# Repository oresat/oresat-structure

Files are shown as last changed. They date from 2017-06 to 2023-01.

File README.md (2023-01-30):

# CURRENT MECHANICAL CAD MOVED TO ONSHAPE

This repository of SolidWorks files is deprecated as of May 2022. After the lauch of OreSat0 to SSO in March 2022, our team decided to move to OnShape because of its collaboration and branching tools. The CAD can be viewed, copied, and exported [here](https://cad.onshape.com/documents/48b910b46086e6b0e2315353/w/4aa305da7933618e47be15b5/e/c74689e568e124e331e7da22).

# DEPRECATED - OreSat Structure Repository - DEPRECATED
The OreSat project is being managed by the Portland State Aerospace Society (PSAS), an interdisciplinary student-led aerospace project in the Maseeh College of Engineering and Computer Science at Portland State University. PSAS is hundred or so open source space nerds, mostly undergraduates of all majors, some graduate students, a few faculty advisors, and mentors we call "industry advisors".

We're building all of OreSat from scratch. For the record, this is a _terrible_ idea. There are plenty of amazing commercial-off-the-shelf CubeSat kits and components out there. But they're not open source, they're a tad bit expensive, and we're an educational group that likes to DIY it anyway. In this repository, you can find the mechanical models of our subsystems: fly them as is, use them as a reference design, or hack them up to make them better! We look forward to seeing what you do with the OreSat bus.

To get started, visit the [Official Site](https://www.oresat.org) and the [OreSat Structure Wiki](https://github.com/oresat/oresat-structure/wiki)

## License 
Portland State Aerospace Society © 2018-2021 

You may redistribute and modify this documentation under the terms of the CERN OHL v2 [http://ohwr.org/cernohl](http://ohwr.org/cernohl).
This documentation is distributed WITHOUT ANY EXPRESS OR IMPLIED WARRANTY, INCLUDING OF MERCHANTABILITY, SATISFACTORY QUALITY AND FITNESS FOR A PARTICULAR PURPOSE. 
Please see the CERN OHL v2 for applicable conditions.

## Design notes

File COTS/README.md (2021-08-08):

# COTS (Commercial Off The Shelf)
Any CAD file for a non-custom part that you downloaded form some website should go in here.
This is basically just a bunch of fasteners and electrical connectors.

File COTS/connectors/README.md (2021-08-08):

# COTS/connectors
This is where you put CAD for electrical connectors.

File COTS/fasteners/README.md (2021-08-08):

# COTS/fasteners
This holds all the COTS parts that hold stuff together.
Part and assembly files shouldn't go in here;
they should go in one of the subfolders according to what kind of fastener they are.

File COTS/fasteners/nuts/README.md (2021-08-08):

# COTS/nuts
This holds nuts. You know what nuts are.
They have internal threads and go on the end of a bolt.
Standoffs are not nuts.

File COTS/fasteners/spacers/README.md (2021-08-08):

# COTS/spacers
This folder holds spacers. Spacers are *not* threaded. Washers are not spacers.

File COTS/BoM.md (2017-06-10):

# OreSat Bill of Materials
_Italic_ prices are variable with quantity. _Italic_ quantities are uncertain (either need to check the model or confer with ECEs).

item number and/or link | extended info sheet | cost per item | quantity per cubesat | description
---|---|---|---|---|---
[SamTec MMCX-J-P-H-RA-TH1][MMCX female] | [here][MMCX female location] | _3.40_ | _66_ | female right-angle radio-frequency connector (all on backplane)
[Samtec MMCX-P-P-H-ST-TH1][MMCX male] | [x][MMCX male location] | _4.58_ | _66_ | male straight radio-frequency connector (3 per card)
??? | [???] | ??? | _20_ | 40-pin female right-angle connector (power and data; 1 per card)
??? | [???] | ??? | _20_ | 40-pin male straight connector (power and data; all on backplane)
??? | [???] | ??? | _10_ | 20-pin female right-angle connector (power and data; _4_&_1_ or _5_ per end card?)
??? | [???] | ??? | _10_ | 20-pin male straight connector (power and data; 1 per solar card)
??? | [???] | ??? | ??? | #4-40 button screw
??? | [???] | ??? | ??? | #4-40 standoff
??? | [???] | ??? | ??? | #0-80 panhead screw
??? | [???] | ??? | ??? | #0-80 standoff
??? | [???] | ??? | ??? | #0-80 micro flat head

[MMCX female]: https://www.digikey.com/product-detail/en/samtec-inc/MMCX-J-P-H-RA-TH1/SAM10615-ND/6561608
[MMCV female location]: MMCX/MMCX_J_P_H_RA_TH1.md
[MMCX male]: https://www.digikey.com/product-detail/en/samtec-inc/MMCX-P-P-H-ST-TH1/SAM10618-ND/6561612
[MMCV male location]: MMCX/MMCX_male_straight.md

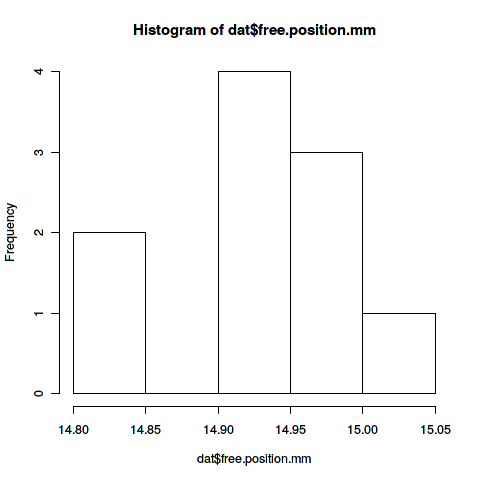
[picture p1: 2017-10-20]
COTS/other/ZFswitches/switchHist.png

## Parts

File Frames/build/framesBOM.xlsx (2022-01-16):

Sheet: 1U
PART NUMBER | DESCRIPTION | QTY.
1U_Frame | Y Frame | 2
1U_Frame | +X Frame | 1
1U_Frame | -X Frame | 1
OreSat_Ca rdWedge | Full Length Card Wedge | 14
+Xframe | +X Card Wedge | 5
OreSat_Ca rdWedgeTri angle | Full Length Card Wedge Triangle | 19
StarTracker Wedge | Star Tracker Wedge Triangle | 2
startracker wedge | +X Startracker Card Wedge | 2
92095A451 |  | 63
93600A061 | M1.5 DIA x 6 DOWEL PIN | 8
92290A060 | M2.5 x 0.45 x 10 Socket Head Screw | 8
91630A221 | M2.5 x 0.45 x 2.5 SCREW-LOCK HELICAL TANGLESS | 8
84985A46 | CPSLO cubesat.org Springs (Using Slotted Long- Nose Spring Plunger 8-36 in CAD) | 4

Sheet: 1.5U
PART NUMBER | DESCRIPTION | QTY.
1.5U_Frame |  | 2
1.5U_Frame |  | 1
1.5U_Frame |  | 1
92703A159 | M2.5 x 0.45 x 8 TORX FLAT HEAD SCREW | 10
92290A060 | M2.5 x 0.45 x 10 Socket Head Screw | 8
91630A221 | M2.5 x 0.45 x 2.5 SCREW-LOCK HELICAL TANGLESS | 8
93600A061 | M1.5 DIA x 6 DOWEL PIN | 8
90910A920 | M2 x 0.4 x 4 Button Head Screw | 69
+Xframecut | +X Card Wedge Cut | 1
+Xframe | +X Card Wedge | 5
startrackerwedge | +X Startracker Card Wedge | 2
OreSat_CardWedgeTr iangle | Full Length Card Wedge Triangle | 19
short | Short Triangle | 6
StarTrackerWedge | Star Tracker Wedge Triangle | 2
OreSat_CardWedge | Full Length Card Wedge | 14
WithCutout | Y Card Wedge Cut | 2
84985A46 | CPSLO cubesat.org Springs (Using Slotted Long-Nose Spring Plunger 8-36 in CAD) | 4

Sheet: 2U
PART NUMBER | DESCRIPTION | QTY.
2U_Frame | +X Frame | 1
2U_Frame | -X Frame | 1
2U_Frame | Y Frame | 2
90910A920 | M2 x 0.4 x 4 Button Head Screw | 111
93600A061 | M1.5 DIA x 6 DOWEL PIN | 8
92290A060 | M2.5 x 0.45 x 10 Socket Head Screw | 16
84985A46 | CPSLO cubesat.org Springs (Using Slotted Long-Nose Spring Plunger 8- 36 in CAD) | 4
92703A159 | M2.5 x 0.45 x 8 TORX FLAT HEAD SCREW | 10
91630A221 | M2.5 x 0.45 x 2.5 SCREW-LOCK HELICAL TANGLESS | 16
OreSat_CardWedge | Full Length Card Wedge | 24
WithCutout | Y Card Wedge Cut | 2
+Xframe | +X Card Wedge | 9
+Xframecut | +X Card Wedge Cut | 1
OreSat_CardWedgeTri angle | Full Length Card Wedge Triangle | 32
short | Short Triangle | 6
StarTrackerWedge | Star Tracker Wedge Triangle | 3
startrackerwedge | +X Startracker Card Wedge | 3

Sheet: 3U
PART NUMBER | DESCRIPTION | QTY.
84985A46 | CPSLO cubesat.org Springs (Using Slotted Long-Nose Spring Plunger 8- 36 in CAD) | 4
93600A061 | M1.5 DIA x 6 DOWEL PIN | 8
92290A060 | M2.5 x 0.45 x 10 Socket Head Screw | 24
3U_Frame | +X Frame | 1
3U_Frame | -X Frame | 1
3U_Frame | Y Frame | 2
OreSat_CardWedge | Full Length Card Wedge | 56
OreSat_CardWedgeTri angle | Full Length Card Wedge Triangle | 63
WithCutout | Y Card Wedge Cut | 4
short | Short Triangle | 12
90910A920 | M2 x 0.4 x 4 Button Head Screw | 219
+Xframe | +X Card Wedge | 7
+Xframecut | +X Card Wedge Cut | 4
startrackerwedge | +X Startracker Card Wedge | 4
StarTrackerWedge | Star Tracker Wedge Triangle | 4
92703A159 | M2.5 x 0.45 x 8 TORX FLAT HEAD SCREW | 10

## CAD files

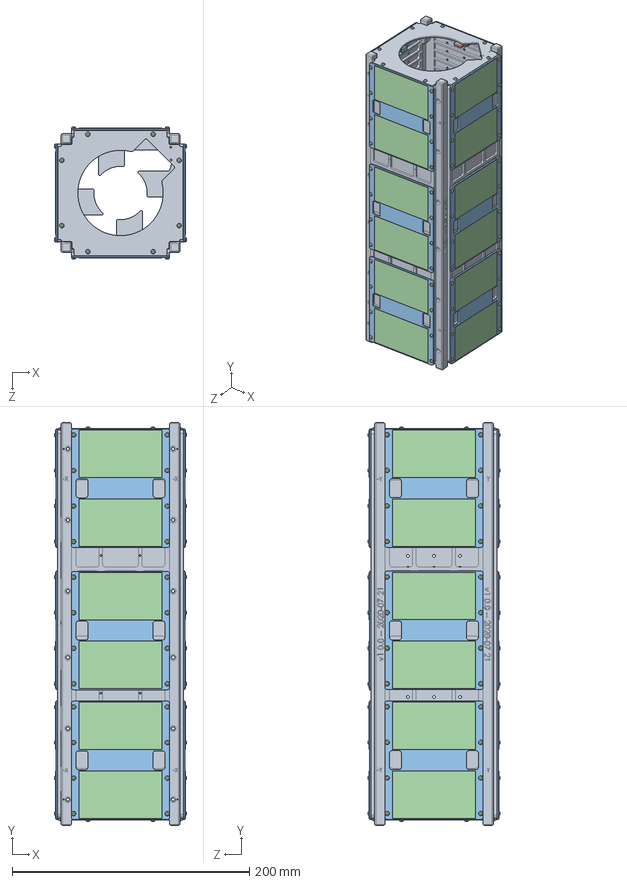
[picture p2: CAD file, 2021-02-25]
3UAssembly.SLDASM
111.4 x 340.0 x 111.4 mm
3U_Frame x 4
BackplaneBoardPCB_3U
M2x0.4x6mm_shoulderScrew_90278A431_18-8 STAINLESS STEEL PRECISION SHOULDER SCREW x 2
90910A920_LOW-PROFILE BUTTON HEAD TORX MACHINE SCREW x 140
Molex, LLC 0733000110 (Backplane) x 87
Molex 73300-0220 (Bullet) x 87
_SFM_120_01_L_D_LC_terminal_2 x 29
_C_20_01_D_pins_4 x 29
_SFM_110_03_L_D_LC_terminal_2 x 27
_C_10_03_D_pins_4 x 27
SolarModulePCB x 12
solarpanel x 24
M55-60212_MOULD.stp x 12
M55-602_CONTACT.stp x 144
M55-700_STRAP.stp x 24
EndCapPCB x 2

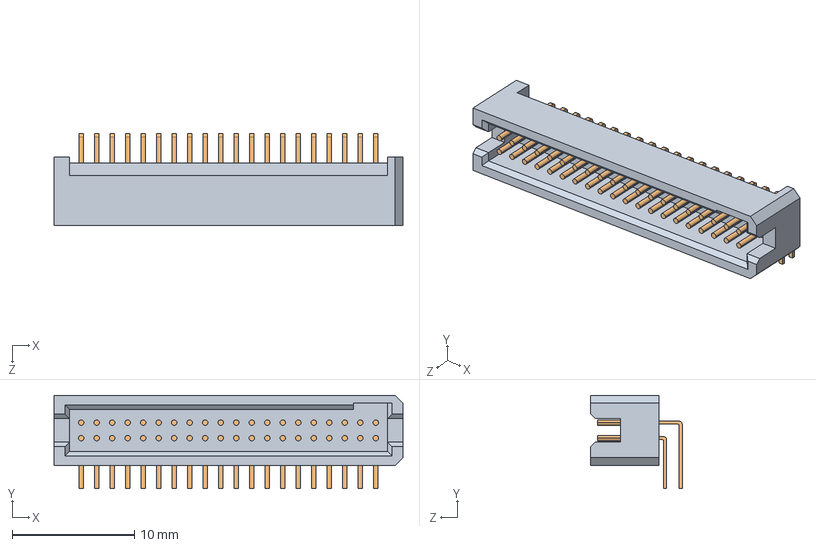
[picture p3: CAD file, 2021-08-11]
ADACS/OreSat0_ADACSCard.SLDASM
28.6 x 7.62 x 7.49 mm
_TFM_120_01_L_D_RA_terminal_2
_TFM_120_01_L_D_RA_pins_4

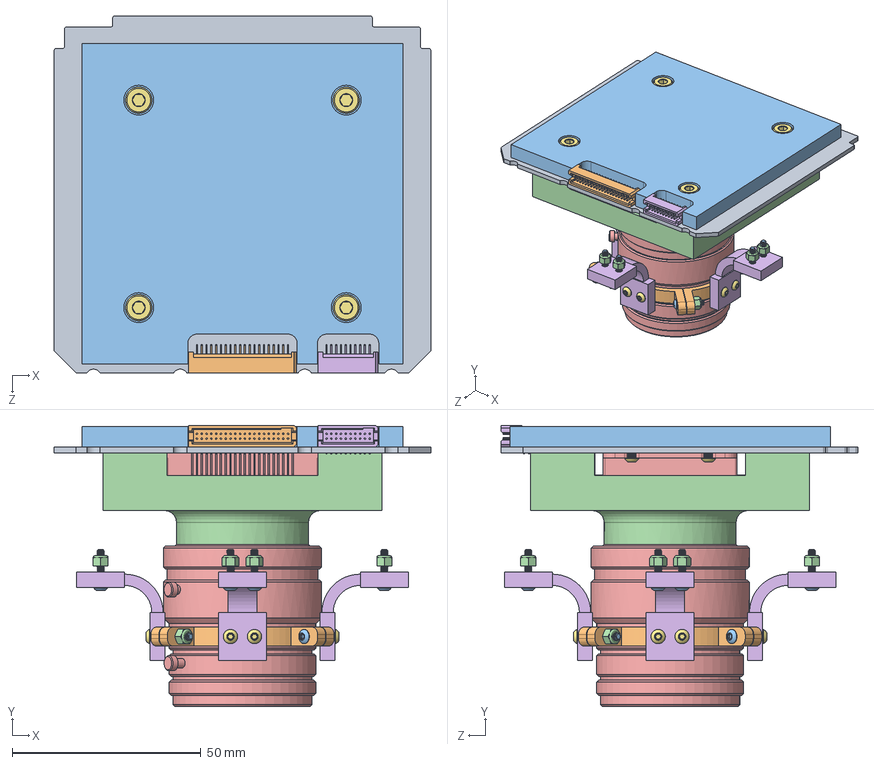
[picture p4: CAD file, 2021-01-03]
AssembledCards/CFCCard.SLDASM
99.8 x 74.5 x 94.6 mm
CFCcard
TFM_120_01_L_D_RA_defeature
CoolerNarrowHoles
lensmount
detector
thermotivestrap x 4
90910A921_LOW-PROFILE BUTTON HEAD TORX MACHINE SCREW x 12
91828A111_TYPE 18-8 STAINLESS STEEL HEX NUT x 4
Filter_Mount
strapclamp x 4
92095A104_BUTTON HEAD HEX DRIVE SCREW x 12
93625A101_TYPE 18-8 STAINLESS STL NYLON-INSERT LOCKNUT x 12
CFClens
TFM_110_01_L_D_RA_defeature
90037A112_METRIC HIGH-STRENGTH 316 SS SOCKET HEAD SCREW x 4

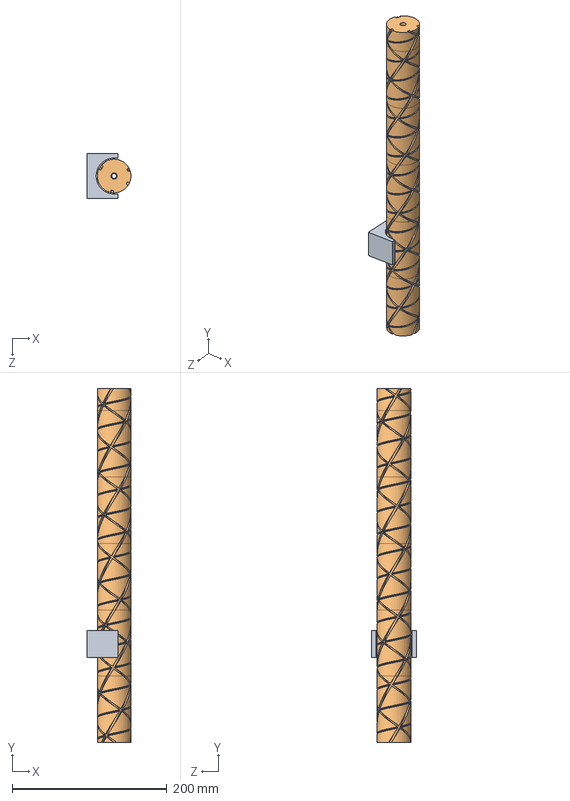
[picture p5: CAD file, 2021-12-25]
AssemblyJig/helicaljig/helicaljig_WithReverseConstraints.SLDASM
56.8 x 457.6 x 58.0 mm
HelicalAntennaSegments_WithReverseConstraint x 6

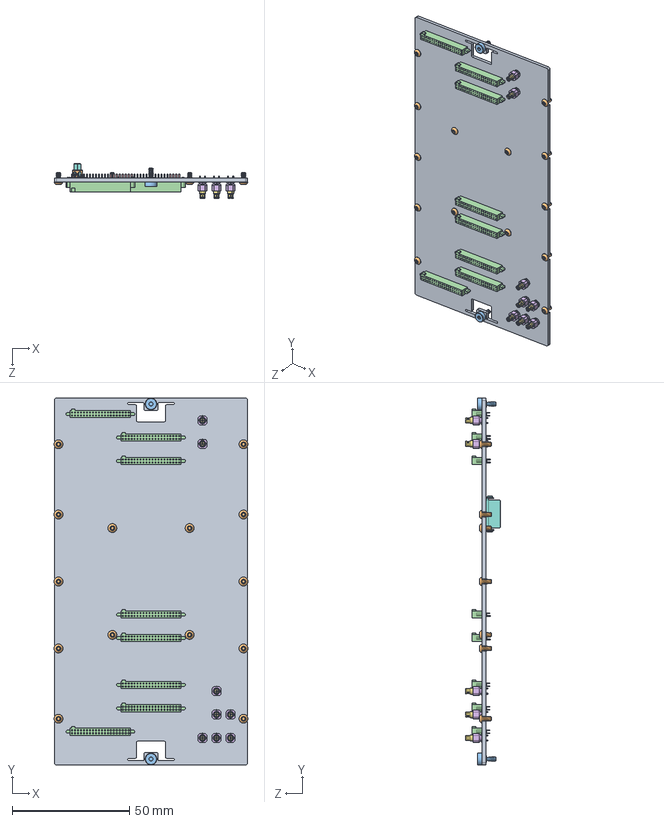
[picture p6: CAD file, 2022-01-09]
Backplane/1.5U_BackplaneAssembly.SLDASM
82.8 x 156.7 x 14.9 mm
1.5U_BackplanePCB
90910A920_LOW-PROFILE_BUTTON_HEAD_TORX_MACHINE_SCREW x 14
90323A421_18-8_SS_LOW-PROFILE_PRECISION_SHOULDER_SCREW x 2
_SFM_120_01_L_D_LC_terminal_2 x 8
_C_20_01_D_pins_4 x 8
Molex, LLC 0733000110 (Backplane) x 8
Molex 73300-0220 (Bullet) x 8
M55-60016_MOULD.stp
M55-600_CONTACT.stp x 16
M55-700_STRAP.stp x 2

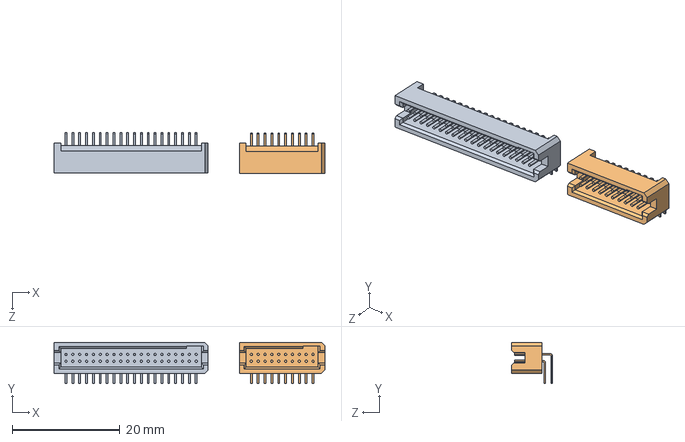
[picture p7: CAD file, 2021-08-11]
Cameras/CFC/OreSat1_CFCOctavoCard.SLDASM
50.2 x 7.62 x 7.52 mm
TFM_120_01_L_D_RA_defeature
TFM_110_01_L_D_RA_defeature

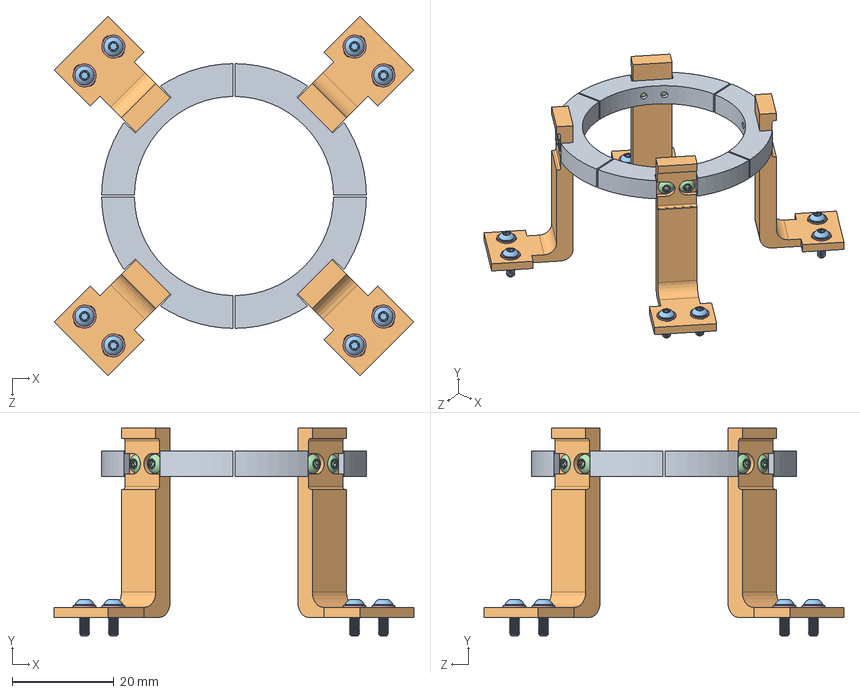
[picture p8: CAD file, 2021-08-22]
Cameras/CFC/thermalStrap/OreSat1_thermalStrapAssembled.SLDASM
70.7 x 40.8 x 70.7 mm
OreSat1_thermalClamp x 4
OreSat1_thermalStrap x 4
90910A922_LOW-PROFILE_BUTTON_HEAD_TORX_MACHINE_SCREW x 8
90910A920_LOW-PROFILE_BUTTON_HEAD_TORX_MACHINE_SCREW x 8
98689A110_ METRIC GENERAL PURPOSE WASHERS x 8

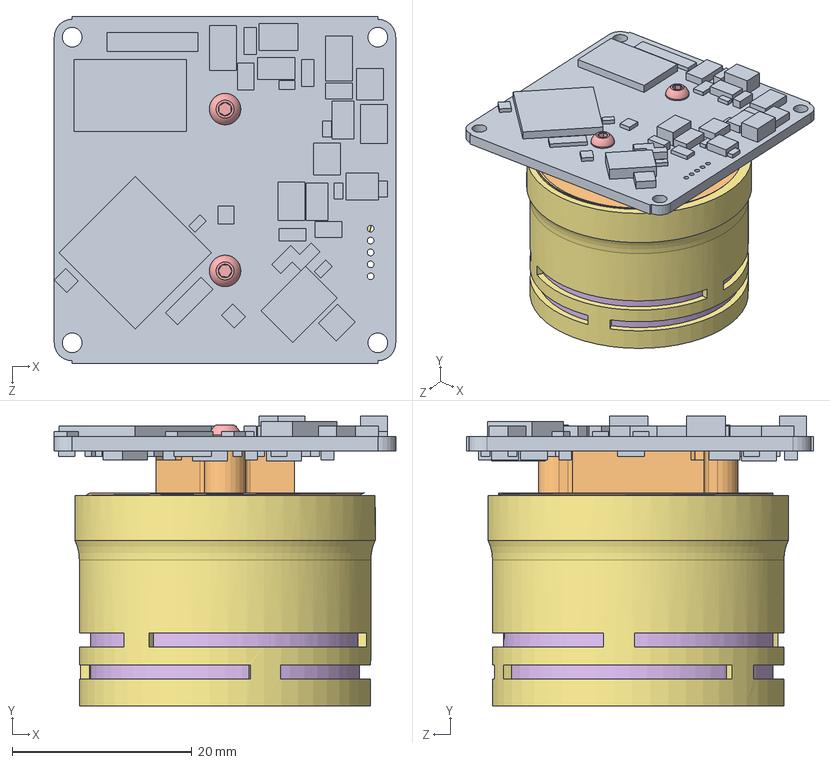
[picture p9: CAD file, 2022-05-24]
Cameras/OreSatLive/OreSat1_OreSatLiveMountBreakdown.SLDASM
38.0 x 32.3 x 38.6 mm
OreSat1_CameraBoard
OreSat1_CassegrainBase
OreSat1_IRfilter
OreSat1_OreSatLiveShim
92095A451_18-8_SS_BUTTON-HEAD_SOCKET_CAP_SCREW x 2
OreSat1_OreSatLiveLensModel
OreSat1_TopSpringOreSatLive

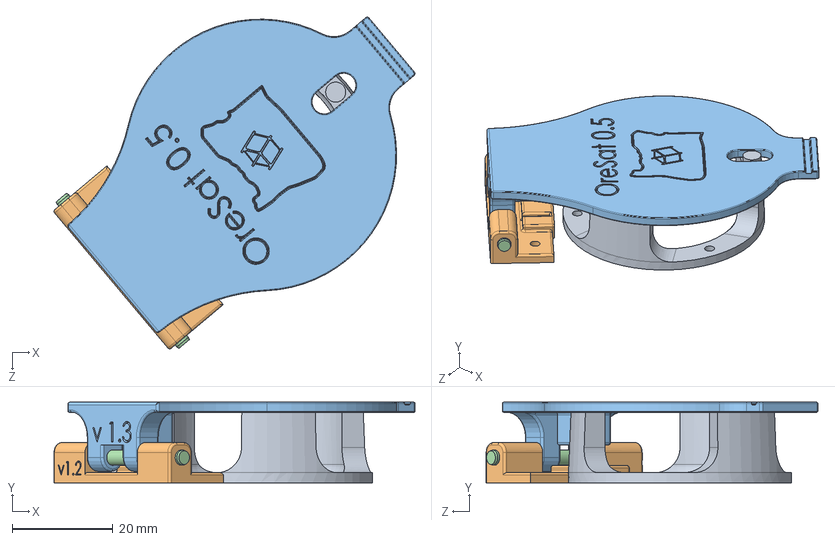
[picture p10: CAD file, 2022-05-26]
Endcard/Helical/OreSat1_HelicalDeployerBiggerSpringBiggerDowel.SLDASM
71.7 x 16.0 x 65.9 mm
OreSat1_HelicalBaseBiggerDiameterSpring
OreSat1_CenterLidBaseBiggerDowel
OreSat1_HelicalDeployerLid
91585A373_18-8 STAINLESS STEEL DOWEL PIN

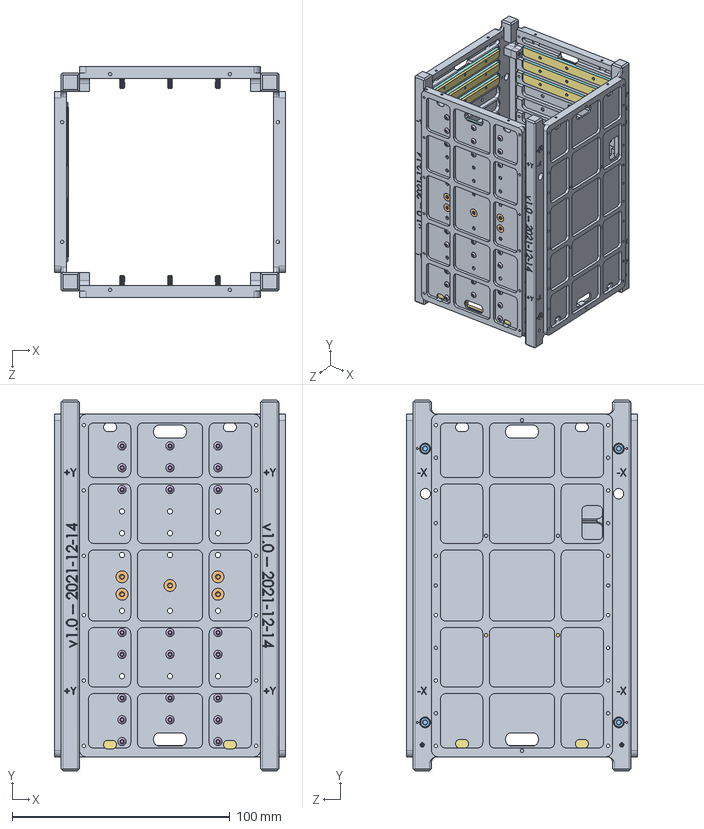
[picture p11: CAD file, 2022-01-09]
Frames/1.5U_Frames.SLDASM
106.0 x 170.2 x 106.0 mm
1.5U_Frame x 4
92703A159_18-8_STAINLESS_STEEL_TORX_FLAT_HEAD_SCREWS x 10
92290A060_TYPE_316_SS_SOCKET_HEAD_CAP_SCREW x 8
91630A221_SCREW-LOCK_HELICAL_INSERTS_WITHOUT_PRONG x 8
93600A061_METRIC_TYPE_316_STAINLESS_STEEL_DOWEL_PIN x 8
90910A920_LOW-PROFILE_BUTTON_HEAD_TORX_MACHINE_SCREW x 69
OreSat_CardWedge x 24
OreSat_CardWedgeTriangle x 27
84985A45_SHORT_LENGTH_SS_LONG-NOSE_SPRING_PLUNGER x 4

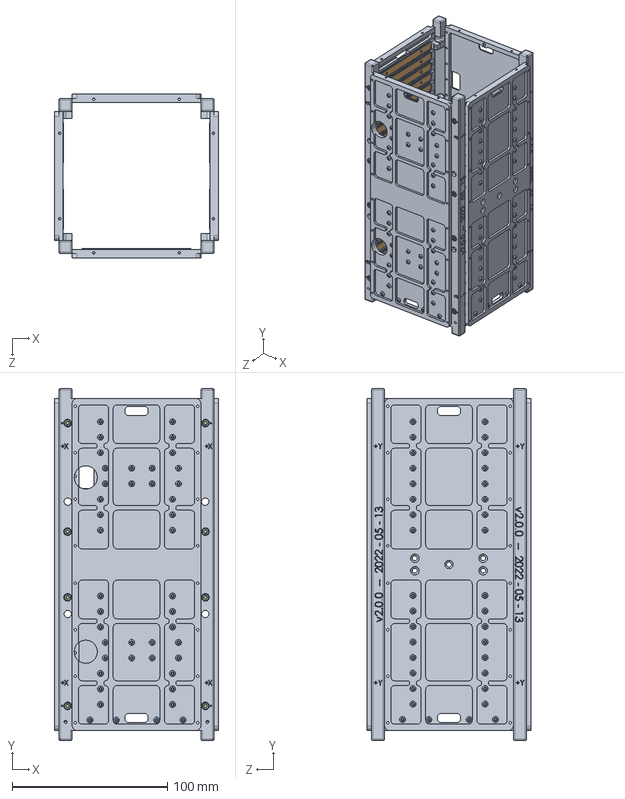
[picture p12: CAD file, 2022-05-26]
Frames/2U_Frames_v2/2U_Assembly_v2.SLDASM
106.0 x 227.0 x 106.0 mm
2U_Frame_v2 x 4
Wedge_v2 x 58
90910A920_Button Head Torx Screws x 116
92290A060_TYPE_316_SS_SOCKET_HEAD_CAP_SCREW x 16

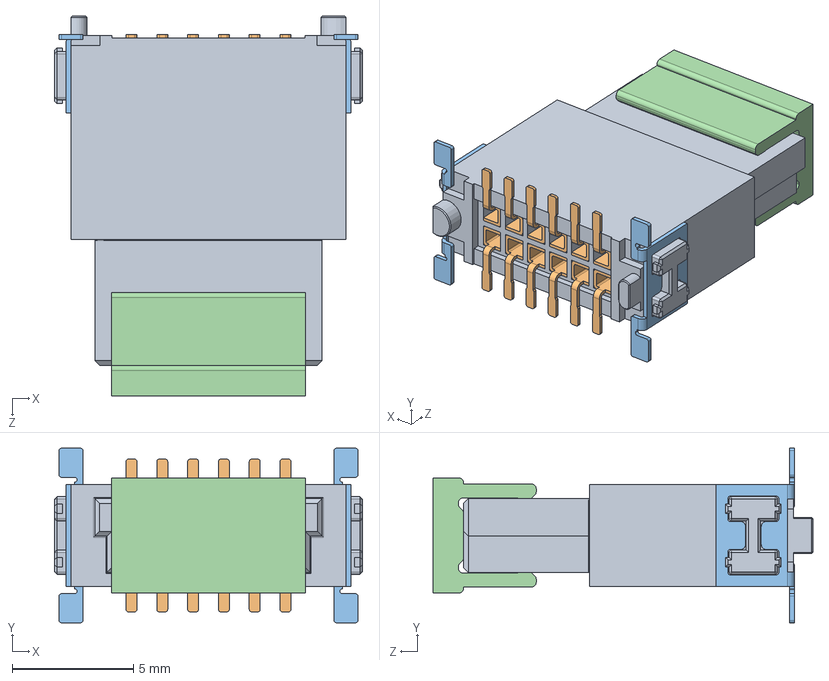
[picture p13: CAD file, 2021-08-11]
HASP/OreSat1B_HASPPowerModule.SLDASM
12.7 x 7.20 x 15.7 mm
M55-60212_MOULD.stp
M55-602_CONTACT.stp x 12
M55-700_STRAP.stp x 2

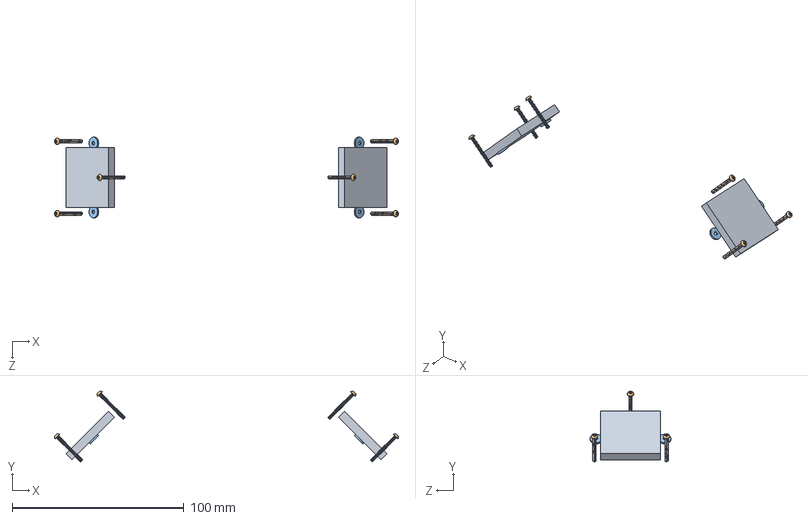
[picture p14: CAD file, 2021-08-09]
HASP/OreSatLivePeriscope/OreSat1B_PeriscopeHASPAsssemblyLarge.SLDASM
200.0 x 41.1 x 47.0 mm
HASPMirror x 2
92095A106_BUTTON HEAD HEX DRIVE SCREW x 6
91116A240_TYPE 18-8 STAINLESS STL OVERSIZED FLAT WASHER x 4

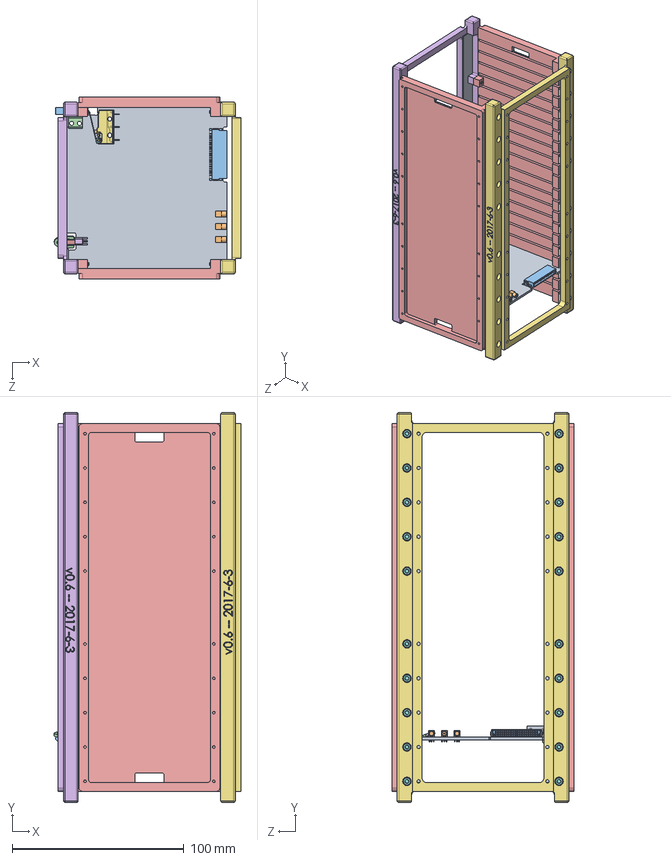
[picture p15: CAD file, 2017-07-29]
InhibitCard/structureOnly.SLDASM
108.6 x 227.0 x 106.2 mm
Inhibit_board
MMCX_J_P_H_RA_TH1 x 3
40pin_female_rightAngle
RBF_tab
MMCX_P_P_H_ST_EM1
MMCX_J_P_H_ST_EM1
db1c-a1lb_1
db1c-a1lb_2
db1c-a1lb_3
db1c-a1lb_4
plungerExtender
plungerGuide x 2
Cuberail_side x 2
Cuberail_front
Cuberail_back
M2.5x10mm_18-8 x 24
spaceFoam x 2

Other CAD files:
Cameras/StarTracker/OreSat_StarTracker.SLDASM
Solar/1.5U_SolarModule.SLDASM
ADACS/OreSat1_ADACSCard.SLDASM
ADACS/ReactionWheels/build/HoleMachining_fixture_assembly.SLDASM
ADACS/Magnetorquers/OreSat_LinearMagnetorquer.SLDPRT
ADACS/Magnetorquers/OreSat_MagnetorquerClamp.SLDPRT
ADACS/Magnetorquers/OreSat_MagnetorquerComplex.SLDASM
ADACS/Magnetorquers/OreSat_ZaxisCopper.SLDPRT
ADACS/Magnetorquers/OreSat_ZaxisFrameMounts.SLDPRT
ADACS/Magnetorquers/OreSat_Zaxiss2.SLDPRT
ADACS/ReactionWheels/OreSat_CableGuide.SLDPRT
ADACS/ReactionWheels/OreSat_EncoderBoard.SLDPRT
ADACS/ReactionWheels/OreSat_EncoderCable.SLDPRT
ADACS/ReactionWheels/OreSat_MagnetHolder.SLDPRT
ADACS/ReactionWheels/OreSat_MotorBracket.SLDPRT
ADACS/ReactionWheels/OreSat_MountingBeam.SLDPRT
ADACS/ReactionWheels/OreSat_RWWeight.SLDPRT
ADACS/ReactionWheels/OreSat_ReactionWheelBoardMounting.SLDASM
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

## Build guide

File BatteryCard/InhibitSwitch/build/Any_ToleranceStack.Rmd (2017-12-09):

---
title: "Inhibit Switch Tolerance Stack"
author: "Joe Shields"
date: "2017-12-08"
output: html_document
---

```{r setup, include=FALSE}
knitr::opts_chunk$set(echo = TRUE)
```

So, I took some measurements with calipers, just listening for when the switch clicked (shown below.)

```{r switchMeasurements}
meas <- read.csv('../COTS/ZFswitches/switchStats.csv')

sdMargin <- 8
peapodSlop <- 1.1
flight.free <- mean(meas$t) + sdMargin*sd(meas$t) 
flight.flushSlop <- mean(meas$t) - sdMargin*sd(meas$t)
flight.flush <- flight.flushSlop-1.1
 
flight.free <-  round(flight.free, 1)
flight.flushSlop <-  round(flight.flushSlop, 1)
flight.flush <- round(flight.flush, 1)
```

```{r plot, echo=FALSE}
par.old <- par(mar=c(4,4,3,0))
layout(matrix(1:2, nrow=1), widths=c(3,1))
posRange <- range(c(meas$t, meas$f, meas$b)) 
plot(meas$label, meas$free.position.mm, pch=1, ylim= posRange, 
     ylab='distance from base of switch (mm)', 
     xlab='switch label'
     )
points(meas$label, meas$trigger.position.mm, pch=2)
points(meas$label, meas$bottom.position.mm, pch=3)
abline(h=c(flight.free, flight.flushSlop, flight.flush), lty=c(3,2,1))
plot.new()
par(mar=c(0,0,0,0))
legend('topright', 
       legend=c('free', 'trigger', 'bottom', 'design free', 'peapod slop', 'design flush'), 
       pch=c(1,2,3, NA, NA, NA),
       lty=c(NA,NA,NA, 3,2,1)
       )
par(par.old)
```

It seems like the spread between the relevant positions is large enough compared to the standard deviation that we don't really need to worry about the statistics of switch production. I set this to give us a comfy $8\sigma$ margin around the switch trigger.

- Set the geometry such that the end of the arm is `r flight.free` mm away from the base of the switch when free of the peapod.  
- Set the geometry such that the end of the arm is `r flight.flushSlop` mm away from the base of the switch when inside the peapod and pushed away from the wall.  
- Set the geometry such that the end of the arm is `r flight.flush` mm away from the base of the switch when inside the peapod and pushed against the wall.  

If you need to shrink that interval, try to keep it centered around `r round(mean(meas$t), 2)`.

[inhibitReqs]: https://docs.google.com/document/d/1oqqp9OsMruQzNAHI35QE_UZxmF_v83l-TLrQsE882ks/edit?usp=sharing

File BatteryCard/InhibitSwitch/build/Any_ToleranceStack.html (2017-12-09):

# Inhibit Switch Tolerance Stack

#### Joe Shields

#### 2017-12-08

So, I took some measurements with calipers, just listening for when the switch clicked (shown below.)

meas <- read.csv('../COTS/ZFswitches/switchStats.csv')

sdMargin <- 8
peapodSlop <- 1.1
flight.free <- mean(meas$t) + sdMargin*sd(meas$t) 
flight.flushSlop <- mean(meas$t) - sdMargin*sd(meas$t)
flight.flush <- flight.flushSlop-1.1
 
flight.free <-  round(flight.free, 1)
flight.flushSlop <-  round(flight.flushSlop, 1)
flight.flush <- round(flight.flush, 1)

It seems like the spread between the relevant positions is large enough compared to the standard deviation that we don’t really need to worry about the statistics of switch production. I set this to give us a comfy \(8\sigma\) margin around the switch trigger.

- Set the geometry such that the end of the arm is 12.9 mm away from the base of the switch when free of the peapod.
- Set the geometry such that the end of the arm is 11.8 mm away from the base of the switch when inside the peapod and pushed away from the wall.
- Set the geometry such that the end of the arm is 10.7 mm away from the base of the switch when inside the peapod and pushed against the wall.

If you need to shrink that interval, try to keep it centered around 12.33.

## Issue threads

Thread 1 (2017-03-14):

Identifying parts from other repos

Joedang, 2017-03-14:
The README mentions that parts from the reaction wheel repo are used. If we don't need to import those from the STEP files, that would probably save a lot of time. I'm going to guess the whole reaction wheel assembly is used?

JSRoland, 2017-03-14:
Yes. I agree.

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

jalouke, 2017-03-14:
The files that are referenced from the structures repo aren't *.step they are *.sldprt and *.sldasm. The dependencies in the top level cubeSAT structure that I created only require that both repos be in the same directory. If that is not the case, then please let me know and I will fix it.

jalouke, 2017-03-14:
I just saw what you meant by step files, and I want to say...

Oh god no, I am not actively a part of OreSAT anymore, but a solid tip about project management, everyone should use the same software when working on a solid model. It is hard enough to make sure there are no conflicts when multiple people are working on the same assembly. It makes everyone's jobs that much harder having to convert files back and forth between different file types, and then praying that there aren't any conversion issues (when converting STEP files to sldprt files, sometimes the part loses surfaces and has to be repaired before it can be used).

Everyone should be using solidworks, or everyone should be using something else. If there is a legitimate concern that Solidworks doesn't have a feature, or there is an easier piece of software to use then by all means switch. However everyone needs to be on the same page.

Joedang, 2017-03-14:
>  everyone should use the same software when working on a solid model.
> Everyone should be using solidworks

Yep.

@calvin-young Did a big rework of the satellite structure in some other program and we're working on porting it into SW so we can all work on it.

jalouke, 2017-03-14:
OK, I think I understand the original question better now. The answer is, it should ultimately be re-made, because I really only drew the version that was originally in the 2U model as a first draft. It also used the original board design as a mounting base (Which if I am not mistaken has changed). The only critical dimensions within the reaction wheel system are the angles of the reaction wheels (check the reaction wheels repo for the correct angles).

Joedang, 2017-03-14:
>  it should ultimately be re-made, because I really only drew the version that was originally in the 2U model as a first draft.

Okay, rad. Thanks.

Closed 2017-03-14.

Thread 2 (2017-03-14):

Migrate from STEP to SolidWorks

Joedang, 2017-03-14:
# SW migration
So, @calvin-young did an awesome refactor of the OreSat structure. Unfortunately, he did it in a different CAD program than most of us. Our task is to migrate that whole assembly into the SolidWorks format.

## How to migrate a part
- If you open [`Rev v0.5/2U_CUBESAT_V0_5.stp`][Rev0.5] in SolidWorks, it will open as an assembly.
  - SW will complain about invalid templates and ask you if you want to use a blank template. Select `Cancel`.
  - Select a template to use. The SW assembly tutorial template or the PSAS assembly template should work fine.
- Go look at the [TODO in the main README](https://github.com/oresat/oresat-structure/blob/master/README.md) and find the first unchecked file.
  - Confirm that the file you're working on hasn't already been migrated. If it has, update the TODO!
- In SolidWorks, find that part in the assembly -- the structure of the TODO matches the structure of the assembly. Right click on it and open the part by itself.
- SW will ask you if you want to automatically identify the features of the part.
  - Just for shiggles, do. It probably won't work but you might get lucky.
    - The goal is for the first feature in the part to _**not**_ be called something like `Imported3`.
- You can try interactively recognizing only certain features that you consider to be the 'last' features and just recursively do that on the 'Imported' feature until you are done. That sometimes works.
  - Most of the features you create will have an associated sketch. You'll need to fully dimension that sketch so that it's all black. If you happen to drag around some not-yet-dimensioned features, make sure to undo those changes.
- Hopefully you won't have to reimplement the part from scratch.
- Now that you have the part implemented, save it with the _**same name**_ as the corresponding STEP file and check it off in the [README](https://github.com/oresat/oresat-structure/blob/master/README.md). It's important that you save it with the _**same name**_ and check it off in the [README](https://github.com/oresat/oresat-structure/blob/master/README.md) so it's easy to tell what's been migrated! It should be self-explanatory where to put your SW file in `v0.5_migrated/`. If you aren't sure, check the READMEs for `v0.5_migrated/` and its subfolders.

## Rebuilding the subassemblies
- Check that _**all**_ of the parts required for you subassembly have been ported to SW.
  - If they haven't, port them! (see above)
  - If they have, feel free to use `git mv` to rename them (Use underscores instead of spaces! Some commands don't do well with spaces.) to something more descriptive, if you want. Make a note in the TODO indicating what they've been renamed to. (If you just rename them rather than using `git mv`, git will think you deleted the file and made another one. Since git operates on the _differences_ in files, this can waste space if your file is large. It would also make it harder to follow the history of the file, if anyone ever needs to.)
- As above, open up [`Rev v0.5/2U_CUBESAT_V0_5.stp`][Rev0.5].
- Right click on the top-level assembly and hide it.
- Unhide the assembly you're building.
- Open a new assembly.
  - Import the corresponding parts which have been ported to the SW format. (I recommend importing the biggest part first, since the first part you import doesn't move.)
  - Proceed to mate the parts together. Preferably, you should use mates which correspond to how the parts would mate in meatspace.
  - Use the STEP assembly as a reference for where stuff goes.
  - If you can still wiggle parts around with your cursor, you probably aren't done mating. ( ͡° ͜ʖ ͡°)
- When your assembly is done, save it with the same name as the corresponding assembly in the STEP file. (This is less of an issue with the assemblies, since the original assembly names and any other names you choose should be obvious.)
- Cross out the subassembly on the TODO.
  - Use double tildes to indicate cross-out: `~~hello world~~` becomes ~~hello world~~.

[Rev0.5]: https://github.com/oresat/oresat-structure/blob/master/Rev%20v0.5/2U_CUBESAT_V0_5.stp "complete STEP file assembly of OreSat version 0.5"

Joedang, 2017-04-29:
Parts people are converting:
* HELICAL CAN
  * Josh
* SPACE FOAM
  * Yohannes
* CARD LOWER
  * Marie
* CARD CAMERA
  * Marie
* ANTENNA SOLARPANEL UNWRAPPED
  * Chris
* coordinate page
  * Marie

jalouke, 2017-04-29:
I totally forgot about the meeting, what time was it?

On Sat, Apr 29, 2017 at 11:25 AM, Joe Shields <notifications@github.com>
wrote:

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

Joedang, 2017-04-29:
Hey @andrewgreenberg, don't forget to add @hmarie2, @RocketmanYG, and whatever Josh Carlson's username is.

andrewgreenberg, 2017-04-30:
All done. I need Josh Carlson's github user's name, there are 5 josh carlsons on github.

Joedang, 2017-05-07:
Hey, @andrewgreenberg, you still need to add @hmarie2.

andrewgreenberg, 2017-05-08:
OMG I AM A TERRIBLE PERSON. Done.

Joedang, 2017-05-13:
Okay, if you were in charge of converting parts in a subassembly, you are now in charge of putting together that subassembly and putting it into the main assembly.

So to be clear, these people are making these subassamblies:
* HELICAL CAN
  * Josh (@paperman5)
* CARD LOWER
  * Marie (@hmarie2)
* CARD CAMERA
  * Marie (@hmarie2)
* ANTENNA SOLARPANEL UNWRAPPED
  * Chris (@wilsoncw6)

Joedang, 2017-05-20:
Mkay, Imma close dis.

Reason: The conversion is done and we've moved on to making changes again.

Closed 2017-05-20.

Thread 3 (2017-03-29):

Part Identification

Joedang, 2017-03-29:
# The Problem
There are a few parts in the OreSat assembly that don't seem to have descriptive names. If someone can identify them, we could probably just find some pre-made SW model. The both have notches, so there's only one way to plug them in. I didn't see any matching connectors when I searched online.  I'm guessing @calvin-young, @andrewgreenberg, or @wrh2 will recognize these. This is of course related to #2.

## 40 pin
This is the 40-pin connector used on most of the boards.
### Male
name in assembly: 100211647UGM000_B.1
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
### Female
name in assembly: 1521040X401XXX_100632479MOD0_1
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

## 20 pin
This connector is used on the solar panels and the backplane.
### Female
name in assembly: 1522020X601XXX_100210477MOD000B
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
### Male
name in assembly: 100211587UGM000_B.2
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

andrewgreenberg, 2017-03-29:
These are two forms of the oreSat card to backplane connectors on OreSat. The 40 pin is what we started with, but quickly moved to the 20 pins. We're currently still on the 20 pins. Males go on the cards, females go on the backplane.

There's no formal name, but you could call them 20pin-oresat-card, 20pin-oresat-backplane, 40pin-oresat-card, and 40pin-oresat-backplane, for example. Those long alphanumeric codes are their generic part names.

Hope that helps?

andrewgreenberg, 2017-03-29:
Note that they came from the manufacturer as STEP files, they were never SW directly.

Joedang, 2017-03-29:
Do you know who makes them? Searching for those part numbers doesn't turn up anything.

andrewgreenberg, 2017-03-29:
They're Harting "har-flex" (seriously?) board to board & mezzanine connectors.

- Harting "Board to Board & Mezzanine Connectors har-flex THR STRAIGHT FEMALE **6.25mm** 40pin PL1", manufacturer pert number (MPN) 15210402401000
   - http://www.mouser.com/ProductDetail/HARTING/15210402401000/?qs=sGAEpiMZZMvlX3nhDDO4AKHv1woNlxZg7ELnbOpcf0U%3d
   - https://b2b.harting.com/ebusiness/app/displayApp/(layout=7.0-12_132_124_140_130&carea=0001400888&citem=00014008880001414518)/.do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

- Harting "Board to Board & Mezzanine Connectors har-flex RA MALE 40pin PL1"
   - https://b2b.harting.com/ebusiness/app/displayApp/(layout=7.0-12_132_124_140_130&carea=0001397574&citem=00013975740001397570)/.do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
   - PL1/PL2 and Tape Reel doesn't really matter
   - http://www.digikey.com/product-search/en/connectors-interconnects/rectangular-connectors-headers-male-pins/1442547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

Joedang, 2017-03-29:
Thank you slack daddy.

Joedang, 2017-10-05:
So, I was putting together the tail card (the thing in position 19 that serves as a mezzanine for the -Z endcap). I grabbed [this model](https://b2b.harting.com/ebusiness/en_us/har-flex-ang-m-12p-PL1-560pcs/15150122601000) (ignore the picture, it really is a 12 pin connector) to go on the tail card and connect to the solar panels on the -Z unit.

It looks like the female connector on the solar panels (bright yellow) is intended to be used with a male connector (dark blue) that has a longer jacket. I couldn't seem to find a longer-jacketed connector on the Harting site though. I think it probably doesn't matter, but it might be a good idea to go find that longer connector.

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

andrewgreenberg, 2019-04-29:
This should all be done by now!

Closed 2019-04-29.

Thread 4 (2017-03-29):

Connector Alignment Between Cards and Backplane

Joedang, 2017-03-29:
#  The Problem
It appears that the connections between the generic board and the backplane are slightly misaligned. The backplane connectors are a little high (0.04 mm to 0.1 mm). I'm not sure how big of a deal that is, maybe the boards are elastic enough to accommodate it; maybe there's something weird about the way the parts were mated; maybe there's going to be more error from the manufacturing.

(obviously related to #2 )

## MMCX misalignment (0.04 mm)
You can also see that the inner conductor of the female connector doesn't have a hole in it, but it appears it should (right center). I'm also not sure if the male connector is supposed to have some barb on it to attach to the barb on the female connector.
The red stuff is interference.
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

## 40 pin misalignment (0.1 mm)
The horizontal alignment is fine (top left), but the vertical alignment is off (right). There's also no hole modeled in the female connector (bottom left). That doesn't really matter, but it could be annoying later on when we check for interference in the assembly.
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

# What to do
Maybe someone like @glennl or @andrewgreenberg will know off the top of their heads whether 0.1 mm is negligible for connector alignment.

We might have to tweak the design of the backplane, which doesn't seem like too big of a deal since it's not in active development right now. I was going to mate the generic board with the rack+backplane so I could figure out which parts of the board are off-limits for components. I was worried that stuff might change, but it looks like this is resolvable by only making changes to the backplane.

# How to close
When someone gets around to fixing those dimensions and the parts are aligned, this issue will be closed.

andrewgreenberg, 2017-03-30:
Ish. We care about things that are > 0.1 mm off. But 0.04 mm? Probably not.

That said, there's no reason to not exactly align them. The backplane  hasn't been fabbed yet, so just go ahead and set the correct height for the connectors on the  backplane. When everything is done, I'll take a drawing and update the eCAD to whatever you specify.

glennl, 2017-03-30:
I think >= 0.1 mm does matter as Andrew said, particularly when thermal
changes and vibration issues come in to play.  It is possible the
connectors ordered are the problem. Often connectors of the same series can
have somewhat different dimensions, ever so slightly. My dream-state tells
me, it would be nice if critical dimensions could be adjusted slightly
during board assembly. ;)

- Glenn

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

jalouke, 2017-03-30:
I think that the through holes for those plugs have more than .1mm slop
(the thickness of a human hair) in them. However it still should still be
fixed, because there is no reason to have "slop" in CAD.

On Mar 29, 2017 6:11 PM, "Glenn LeBrasseur" <notifications@github.com>
wrote:

I think >= 0.1 mm does matter as Andrew said, particularly when thermal
changes and vibration issues come in to play. It is possible the
connectors ordered are the problem. Often connectors of the same series can
have somewhat different dimensions, ever so slightly. My dream-state tells
me, it would be nice if critical dimensions could be adjusted slightly
during board assembly. ;)

- Glenn

On Mar 29, 2017 17:06, "Andrew Greenberg" <notifications@github.com> wrote:

> Ish. We care about things that are > 0.1 mm off. But 0.04 mm? Probably
not.
>
> That said, there's no reason to not exactly align them. The backplane
> hasn't been fabbed yet, so just go ahead and set the correct height for
the
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

> Reply to this email directly, view it on GitHub
> <https://github.com/oresat/oresat-structure/issues/4#
issuecomment-290263078>,
> or mute the thread
> <https://github.com/notifications/unsubscribe-auth/AB2tbKPFL7jringO4T809J-
G4J_dOkkRks5rqvIOgaJpZM4MtszW>

> .
>

—
You are receiving this because you are subscribed to this thread.
Reply to this email directly, view it on GitHub
<https://github.com/oresat/oresat-structure/issues/4#issuecomment-290272545>,
or mute the thread
<https://github.com/notifications/unsubscribe-auth/AGxHjbuSCtSbxlmK5s0gtzHaj0eu2h2Sks5rqwFVgaJpZM4MtszW>
.

Joedang, 2017-03-31:
> it still should still be fixed, because there is no reason to have "slop" in CAD.

Yeah, I'll add a note to the backplane in the TODO. It seems like it should be pretty straight forward to fix.

Joedang, 2017-05-21:
So, tiny update to this. It was unclear _which_ model/manufacturer of MMCX connectors were used. AFAIK, @jalouke made the models for the connectors based on a manufacturers diagrams. Since I wasn't sure of the model/manufacturer, I'm saying these ([male](https://www.digikey.com/product-detail/en/samtec-inc/MMCX-P-P-H-ST-TH1/SAM10618-ND/6561612), [female](https://www.digikey.com/product-detail/en/samtec-inc/MMCX-J-P-H-RA-TH1/SAM10615-ND/6561608), [TDS](http://suddendocs.samtec.com/catalog_english/mmcx.pdf), [male CAD](https://www.samtec.com/partnumber/mmcx-p-p-h-st-th1?vendor=digikey), [female CAD](https://www.samtec.com/partnumber/mmcx-j-p-h-ra-th1?vendor=digikey)) are canon. They are also Greenberg approved.

jalouke, 2017-05-22:
they should be named after their respective part numbers on digikey.

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

Joedang, 2017-06-04:
I looked around some of the older commits. It seems the MMCX connectors either have a generic name or aren't used in the assembly. If there's no strong reason to seek out what's in the model, I'm just going to replace them with the Samtec connectors.

andrewgreenberg, 2017-06-04:
Actually, not the digikey part number, but the <manufacturer>-<manufacturer's part number>.

Also the Samtec connectors *are* MMCX connectors... so maybe we should name the parts mmcx-samtec-<partnumber>.

Joedang, 2017-06-04:
The file names that Samtec gave the connectors are `MMCX_P_P_H_ST_TH1.SLDPRT` and `MMCX_J_P_H_RA_TH1.SLDPRT`, so I'm just gonna leave them like that.

Reason for closing: misalignments have been fixed.

Closed 2017-06-04.

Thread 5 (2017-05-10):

Clean up Directory Structure

Joedang, 2017-05-10:
## The Problem
Having all the design versions in different directories *while already being part of the repo* is silly. This is what Git is for.

## Proposed Solution
- [X] For every revision `n`:
  - ~~[X] Go through the commit history and find the *first commit* where the `Rev v0.[n]` directory  appears.~~
  - ~~[X] Tag the commit *before that* as release `0.[n-1]`.~~
  - [X] In all cases, there's a commit that says when the revisions are. Just go by that, I guess.
- [X] Start a "cleanup" branch.
- [X] Remove all the old revisions.
- [X] Move the contents of `v0.5_migrated` to the top-level directory.
  - [ ] Remember to open the assemblies and re-link any parts which SW lost track of.
- [X] Wait until the structure is completely migrated into SolidWorks.
- [X] Merge  `cleanup`  into `master`.  (#7)
- [X] Tag as release `v0.6`.
- [X] Close this issue.

## Remarks
The reason for waiting to change the directory structure until after the conversion is convenience. I could do it on another branch, but I'm not sure how Git would handle binary files which were changed on one branch and moved on another. It's also convenient to have the old and new models available at the same time during the conversion.

andrewgreenberg, 2017-05-11:
This would be amazing. Go ahead and tag it as something higher, like 0.6 or even the dreaded 1.0. We're done playing around, I think we're close enough that we really have something here.

Joedang, 2017-05-12:
I was thinking the criterion for `1.0` would either be "most/any changes would force other projects to change their work" or "this is something that might actually fly". The main things I would not call "1.0" are the turnstile antenna and the camera mounting.

Joedang, 2017-05-18:
The assemblies still need to be updated to point to the new file locations, but that should just happen automatically as people open them.

Closed 2017-05-18.

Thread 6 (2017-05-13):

Redesign OreSat -Z (turnstile) Antenna

Joedang, 2017-05-13:
## The Problem
The antenna mounting/deployment design that's currently in the model isn't machinable and uses too small of a bending radius.

## Proposed solution

There's a notebook of relevant calculations [here](https://github.com/oresat/oresat-structure/blob/master/v0.5_migrated/Zneg/antenna_bending.ipynb) (location will change soon).

- [ ] Add a bending energy calculation to the Jupyter notebook. Find:
  - [ ] How much energy is in a coiled-up antenna.
  - [ ] How much energy is in a folded antenna.
  - [ ] Angular impulse from antenna deployment. (optional)
- [ ] Preliminary CAD design of how the antenna will mount/fold. (@paperman5)
  * Ideally, should be made of FR4 and/or G10 and machined in a single operation/fixture on a PCB router.
- [ ] Determine an acceptable failure rate for the deployment.
- [ ] Mechanical testing of deployment mechanism.
  - [ ] Bench-top testing.
  - [ ] Migrogravity testing in the DDT.
- [ ] Electrical testing. (@glennl)

Some iteration on this design may be required.

## Critera for closing this issue
- [ ] Mechanical testing has been done.
- [ ] Deployment failure rate is below the acceptable rate.
- [ ] Electrical performance is acceptable. (@glennl)

Joedang, 2018-01-23:
So, this is a capstone now. #underestimation

This may be of mild historical interest to @calvin-young, @Paijanne, @shivadeath, @Burris94, and @jgeorge12.

Closed 2018-01-23.

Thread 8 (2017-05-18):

Helical Card Connector Locations

paperman5, 2017-05-18:
The helical card subassembly in the old step assembly of the satellite has multiple connectors phasing through geometry without the appropriate cutouts.
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
I am not sure if all of these connectors are supposed to be where they are currently placed. Could someone with some electrical knowledge of the satellite give some input? For the new assembly I will only add the connector on the bottom of the plate for the time being.

paperman5, 2017-05-18:
@Joedang or others, would you mind referring some people who might know about this issue?

andrewgreenberg, 2017-05-18:
Me! Talk to me!

I assume those are connectors for the solar panels. So yes, they're still there. However, is this an end cap, or an actual card? Can you come Friday 2pm - 5pm to discuss?

Joedang, 2017-05-19:
@paperman5 Yeah, those are for the solar panels. If you take a gander at the v0.5 assembly, they match up with the connectors coming out of the plane of the solar panel boards.

@andrewgreenberg I think this is showing the 2nd-to-last card on the +Z end. I assume we don't want the helical antenna to be connected to its ground plane though. I guess we have details to work out on both antennas.

paperman5, 2017-05-19:
@andrewgreenberg @Joedang I won't be able to make it to the Friday meeting, although I might be able to jump on Hangouts for a while. This is the last card that I see on the end of the old step assembly, though there's probably a cap that goes over it. If the connectors need to be there I can include some cutouts in the part, but I imagine that would make the card harder to manufacture.

That's the way the antenna was attached in the old assembly, I can change it once we get some feedback.

paperman5, 2017-05-31:
Closing this since the antenna is being redesigned so this isn't relevant anymore

Closed 2017-05-31.

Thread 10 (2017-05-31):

Helical Endcap Fastening

paperman5, 2017-05-31:
There is currently no way that I see for the helical antenna end cap to be fastened to the end of the satellite:
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
A possible way to fix this would be to add supports underneath the endcap coming out of the sides of the rail assembly. However I need to confirm that this is allowable as I am not sure of the rail requirements and it would impose some (still generous) vertical restrictions for the solar panel card that I believe goes under the endcap. I was thinking something like this:
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
Does this seem reasonable? If it does, I will go ahead and make these changes.

andrewgreenberg, 2017-06-01:
Huh, this is an interesting problem. First, the end cap has to be mostly a solid PCB, since it's the ground plane for the helical antenna. Second, the helical antenna can't be "embedded" in the PCB, it has to go start from that ground plane. So you'll have to drop the end cap "into" the satellite body if you need more than the 6.5mm height from the top of the frame to the top of the rails.

Your proposal seems fine to me. I approve if Joe approves. One thought: can we squish "out" the coiled up helical so it fits in the 6.5 mm space? That means slightly "unwinding" the helical as it gets compressed, but that seems OK?

Joedang, 2017-10-06:
So, I made some endcap boards that just sit on top of the structure. They screw into the rack and register with the rails with 0.1 mm of clearance (so, 0.2 mm of slop in X and Y).

It's worth noting that with the mezzanine connections to the head/tail cards (see #12 and #13), we loose some real estate for antennas.

## +Z face:
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

## -Z face:
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

## -X corners:
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

## +X corners:
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

Joedang, 2017-10-07:
Update from the Greenberg:
Osh Park guarantees features that can be done with a 0.1" (yes, 1/10 inch, not 0.1 mm) endmill. So, the dogbones would need to be no larger than 0.05" (1.27 mm) in radius. I think they're 1 mm in radius right now, so I'll have to go in and change them.

Joedang, 2018-01-23:
I updated the radius of the dogbone fillets. The original issue has been addressed, and I assume that any if additional changes are needed, they will be brought up by the capstone. [So, here I go closing again. ](https://youtu.be/YG6DifUtPvs)

Closed 2018-01-23.

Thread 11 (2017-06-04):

Choose/Design Inhibit Switches

Joedang, 2017-06-04:
There was some good discussion on how to do the inhibit switches in the hangout today, so I kind of want to capture what we worked out and what needs to be worked out in the form of an issue.

# Problem
The Nanoracks spec requires us to have inhibit switches. We don't have any in our design yet.

Inhibit switches are similar to the remove-before-flight pin. They keep the satellite from turning on. When the satellite is in the peapod, the switches are activated (presumably in a way that crowbars satellite power). When it gets launched, the switches pop out into the closed state, giving power to the satellite. After waiting 30 minutes, a simple board on the satellite tells everything to start turning on.

## [Requirements as per the Nanoracks SRD-029 section 4.7 (page 12)][SRD-029]:
* We need at least 3 inhibit switches.
* They can be pushers in the -Z rail ends, or roller/sliders in the sides of the rails.
* Any roller/sliders must be at least 75% of the width of _the deployer's guide rail_, aka at least 1.875 mm (much smaller than we thought when discussing on the hangout).
* The switches cannot exert more than 3 N. (That's 305 grams-force, for anyone searching Digi-Key.)

It's worth noting that the spec doesn't say if that 3 N is the _total_ force of all the switches or for a single switch. Two of them will likely be on opposing faces though, so it's a moot point.

# Initial thoughts/solutions
Everyone basically agreed that putting switches in the -Z ends of the rails would be awful.

The thought for a while was that we could embed lever-style limit switches (like those typically seen in 3D printers or laser cutters) into the rails. However, this would be a kind of big change to the structure of the satellite and require weird changes to the card slots and a very custom board(s).

We thought about using "cross roller plunger switches", but they're all kind of huge and would require big cutouts from the structure. "Simulated rollers" were also a nice option, but violate that 75% rule.

The general consensus between @andrewgreenberg, @jalouke, @paperman5, and @joedang at the end of the hangout seemed to be that we should use a plunger or lever switch on one of the boards and make an extender for it. The extender would go through a hole in the rail. (see below)

# Mockups
I made a thing in SolidWorks to get an idea of how we might implement the inhibit switches in OreSat.

I used [Panasonic's ESE-11SH1C][SH1C] and designed for a 1.5 mm travel. (The [ESE-11SH2C][SH2C] may also come in handy if we choose to use that switch.) The data sheet for the switch says it triggers at 0.75 mm and bottoms out at 2.4 mm. We can't really make the travel more than 2 mm, otherwise we'll either have a chance of the switch sticking when it goes to uninhibit mode or when it's inserted into the peapod. (see 2nd and 5th images for clarification)

Using this style of switch, we can add a spring if we want more force.

We would need to clip the leads of the switch after soldering it into the board, otherwise they would collide with the rack. That's NBD.

If we want to center the plunger on the plunger extender (I do), we'll have to make a cutout in the card rack to accommodate it. The extender is already centered on the rail. The extender _must_ be centered on the peapod guide rail. AFAIK, the guide rail is centered on the cubesat rail (Figure 9 in SRD-029 seems to agree. Someone please give me a sanity check here.)

## uninhibited state:

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

### inhibited state:

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

# Action to take
* Since @hmarie2 has been reading about switches, maybe she can determine whether or not this would be an acceptable switch to use and/or look for alternatives.
* If we do want to do something like this, we should think about where all the limit switches will go, since they will need corresponding cutouts in the rails/rack.
* We should consider how we would go about manufacturing a plunger extender and making the cutouts in the rails/rack. (eeny-weeny engraving endmill and CNC, probably)
* How can we reduce the chance of the switch sticking?
* Is this switch non-weeny/low-resistance enough for the ECEs? (I'm assuming it's not really a high-power deal.)

[SRD-029]: https://drive.google.com/open?id=0B_LcfbAtlfiZQkhqN1R0VHQybFU
[SH1C]: https://www.digikey.com/short/3dbb78
[SH2C]: https://www.digikey.com/short/3dbb31

Joedang, 2017-06-04:
Also, side note, is this sort of thing more appropriate as an issue or a project?

jalouke, 2017-06-04:
I think we were mistaken when we were discussing the size of the portion in
contact with the P-pod. I believe it needs to be 75% of the with of the
P-pod rail, not the cubeSAT rail ( 75% of 2.5mm).

On Jun 3, 2017 6:05 PM, "Joe Shields" <notifications@github.com> wrote:

Also, side note, is this sort of thing more appropriate as an issue or a
project?

—
You are receiving this because you were assigned.
Reply to this email directly, view it on GitHub
<https://github.com/oresat/oresat-structure/issues/11#issuecomment-306010812>,
or mute the thread
<https://github.com/notifications/unsubscribe-auth/AGxHjeOaLivzpZUsQOTB33SakWEI4JCJks5sAgLggaJpZM4NvPj_>
.

Joedang, 2017-10-06:
A little bit of an update to this issue:
We picked out some reasonable switches. (They're a bit big, but smaller switches just have too small of travel.) Based on the manufacturer's data sheet, various travel distances of the switch are good but the tolerance is too loose for what we need. We ordered some of them and it looks like they reported very conservative tolerances. (In reality, they are much tighter.) I went through and measured the actuation positions with calipers (not sure if I pushed that data). It would be nice to redo that with a micrometer.

I still need to do the tolerance stack to get the ideal dimensions for the plunger, bracket, and mounting holes. (Maybe I should make a notebook for that? I did it as a SW drawing, but that turned out to be almost useless.)

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

andrewgreenberg, 2019-04-29:
This is now Oleg's! Not sure if the above discussion is useful, but just in case.

catiespivey, 2019-09-25:
Can we close this since the design is done? Just waiting on you and David to do testing @andrewgreenberg

Closed 2020-07-12.

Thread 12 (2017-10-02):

RF connections to +Z and -Z endcaps

Joedang, 2017-10-02:
# Problem
We need a good way transfer RF between the backplane and the endcaps (you know, half of the sinks/sources of RF on the satellite). The backplane can't reach the top side of the +Z endcap and the connectors that *would* go to the -Z endcap interfere with the -X frame. Here's a screenshot of the MMCX connectors that *would* connect to the + side of the -Z endcap (legs of the MMCX connectors interfere with the frame):

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

# Possible solutions
We could reach the bottom side of the -Z endcap if we make a cutout in the frame or cut the legs of those MMCX connectors to be hecka stubby. We might be able to remove the MMCX connectors from the card 0 (directly below the +Z endcap) and add some to the bottom of the +Z endcap. (This would amount to a scooch in the +Z direction for the holes for the card 0 MMCX connectors on the backplane, to redirect them to attach to the +Z endcap.)

# Needed action
I'd like an opinion from @glennl and/or @andrewgreenberg. Would it be feasible to modify the MMCX connectors on the backplane (just in the -Z endcap position) so they don't stick out the back? I'm guessing we strongly want to avoid card-to-endcap connections, since we can't slide in a card-endcap pair (endcaps screw, but don't slide).

andrewgreenberg, 2017-10-02:
Since the "end" cards are used to attach the solar panels, it can't just be pulled out like all the cards -
 the side solar panels have to be removed first. I suggest we continue this trend, and make the Z endcaps veritcally plug directly into the "end" cards. So you'll need to remove the two side solar panels AND the Z endcap to remove that top (or bottom) card.

Joedang, 2017-10-06:
Reason for closing:
We're going with inter-board connections between the head/tail cards and the endcaps, making the head/tail cards big mezzanines between the backplane, solar panels, and endcaps.

Joedang, 2017-10-06:
Update:
This is the sort of shenanigan I went with. Note that this is definitely not the final design, since #13 is still a thing.

## tail card (mezzanine to -Z endcap):
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

Closed 2017-10-06.

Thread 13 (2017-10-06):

spacing between head-tail cards and endcaps

Joedang, 2017-10-06:
# Problem
The head and tail cards (position 0 and 19, respectively) are too far apart for the connectors to reach the endcaps without modification.

Here, you can see the 20 pin connectors on the -Z endcap *just barely* connect. They need a 2 mm boost (similar story for the +Z):
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

Similarly, the MMCX connectors between the boards (shown below) need a 4 mm boost:
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

# Proposed solution
We could have a little "booster seat" board that sits underneath one of the 20 pin connectors, and have a similar thing on both ends of the MMCX connectors. I would imagine you could just solder it to the larger board along with its connector.
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
I'm not sure if that's a sane thing to do electrically or vibrationally. Do any electrical people have thoughts on it? ( @eyand @andrewgreenberg @glennl @aSmig )

aSmig, 2017-10-06:
I don't like it.  This results in solder connections that we can't inspect.  It may not be so important with the 20-pin connector if the booster seat is soldered around castellated edges.  But the RF connector is much more sensitive to pointy solder formations hidden between boards.

What would it take to move those boards closer together?  Why are we considering using board to board connectors with different mated heights?  Are there taller variants of these parts?

andrewgreenberg, 2017-10-06:
I agree with Kenny; a good idea Joe, but not one we should do. What is the actual spacing between boards?

Joedang, 2017-10-06:
> What would it take to move those boards closer together?

Right now the slot, the holes for the connectors, and the connectors are
the starts of arrays. So, the array would need to be moved and individual
features added. It wouldn't be hard to do, but it kind of sucks adding
exceptions...

> Why are we considering using board to board connectors with different
mated heights? Are there taller variants of these parts?

These are just the connectors that are used for everything else. I haven't
looked for taller connectors. If we can use something that works without
moving the boards, that would be ideal.

> What is the actual spacing between boards?

The array is spaced at 10 mm. So 8.4 mm between the boards.

On Oct 6, 2017 2:02 AM, "Andrew Greenberg" <notifications@github.com> wrote:

I agree with Kenny; a good idea Joe, but not one we should do. What is the
actual spacing between boards?

—
You are receiving this because you were assigned.
Reply to this email directly, view it on GitHub
<https://github.com/oresat/oresat-structure/issues/13#issuecomment-334699897>,
or mute the thread
<https://github.com/notifications/unsubscribe-auth/AQFJ4I0qlOPjJHJjpRKe_PcRuaXCAaFqks5spezBgaJpZM4Pv__0>
.

Joedang, 2017-10-06:
Correction:
The spacing between the head/tail cards and the endcaps is actually 10 mm, not 8.4 mm.

andrewgreenberg, 2017-10-06:
Excellent! OK, then this means that we can get 20 pin connectors that will do exactly 10 mm, and now we just need to find 10 mm RF connectors. Will do!

Joedang, 2018-01-23:
At this point, it seems like the antenna capstone _probably_ won't put electronics on the endcaps. So, I'm going to close this, as it's not really relevant anymore.

Closed 2018-01-23.

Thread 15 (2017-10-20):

Consolidate Hardware/ and COTS/

Joedang, 2017-10-20:
Some COTS parts are still in the old `Hardware/` directory.

# Background
When converting the model from STEP to SoidWorks (v0.5 to v0.6), all/most of the COTS stuff was in `Hardware/`. Later, we started using `COTS/`. We also started using sub-directories a little more liberally and prepending human-readable names to the manufacturer-provided file names.

# The Problem
We need to get everything into `COTS/`, using consistent file/directory naming. We need to make sure that the exact manufacturer part numbers can be inferred from the file names. We need to remove any unnecessary files.

# Proposed Solution
For each file in `Hardware/`:
* Check if it's used somewhere in `OreSat.SLDASM`.
    * If it isn't, remove it.
* Try to find the part on McMaster, Digikey, or whatever is relevant.
    * If you can't find it, try to find an equivalent part.
* If the manufacturer gave a bad name to a file, use the format `SIZE_TYPE_MATERIAL_MFGNUMBER.extension`. For example, `M3x5_buttonHead_18-8stainless_12345ASDFG.SLDPRT`. (The MMCX connectors are an example of when the manufacturer's file name is acceptable, and we don't need to change it.)
* Move the file into `COTS/`.
    * If there are similar parts, make a subdirectory in `COTS/` and put them in there. (For example, fasteners of the same size.)
* Rebuild `OreSat.SLDASM` to tell SW where the part is located.
* Check if the part appears in the BoM.
    * If not, add it.

# Criteria for Closing
Everything has been removed from `Hardware/` and we can rebuild `OreSat.SLDASM` without any missing part errors.

Joedang, 2018-08-05:
This is practically not a thing any more, since I've replaced all the fasteners. It's also a bullet point in #25 .

Closed 2018-08-05.

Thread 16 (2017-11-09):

Thin features in aluminum structure

Joedang, 2017-11-09:
The front, back, and side parts of the rack have thin features (~0.4 mm).

# Background
So, we want to make an aluminum prototype of the structure (and, of course, the final thing will be aluminum). I sent a quote to ProtoLabs to see how much that would cost. The thin features in the sides were deemed unmachinable, while the front/back frames had warnings for thin features near the larger screw holes and for some unmachinable inside corners near the 45 degree faces.

#### sectioned view of the slots (0.4 mm wall):
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

# The Problem
We kind of need an aluminum prototype and definitely need a structure that doesn't have dangerously thin walls.

Also, it's unclear how much mass we can add to the structure. (Any estimates on how massive the batteries, reaction wheels, and electronics will be are going to be really rough.)

# Proposed Solution
- [ ] Thin walls on the slots
  - [ ] Find out if there is a minimum wall thickness that ProtoLabs will allow.
  - [X] Make the pocket on the opposing side of the slots shallower.
- [ ] Inside corners on the 45 degree faces
  - [ ] AFAIK, adding small fillets to those corners wouldn't interfere with anything. Add fillets there and check for interference with the boards.
- [X] Thin walls near the screws
  - [X] Switch to screws with a smaller head. (@andrewgreenberg  may get his wish for a single screw size.) This may mean adding more screws. (Reminds me that we should have some quantitative method for choosing the number of screws that attach the front/back frames to the sides.)
- [X] Mass budget
  - [X] Ideally, we can keep the mass of the structure constant. We can add cutouts to the material between the slots.

# Criteria for Closing
This should be closed when ProtoLabs no longer complains about the issues mentioned here.

Joedang, 2018-01-13:
## Update
In some recent changes, I
- Made the pocket shallower, to bulk up that thin-wall feature from 0.4 mm to 1 mm.
- Switched to slightly smaller-headed screws to avoid the thin feature for the counter-bores.
- Added cutouts to the slots, to reduce the mass.

v0.8 rack mass: 496.8 g
rack mass before changes: 552.7 g
reduction: 55.9 g (10.1%)

Joedang, 2018-01-23:
Protolabs no longer complains about the thin features. The 45 degree chamfers still end up getting filleted, but since that doesn't effect anything, I don't care. They also won't machine the engraved labels. Again, don't care enough. They aren't required for the flight article and we can just write on the engineering/prototyping models.

Closed 2018-01-23.

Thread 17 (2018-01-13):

Update clearance call-outs in generic board drawing

Joedang, 2018-01-13:
# Background
The pillars and screw holes that join the frames reduce the clearance for components in certain areas on certain boards. There's a technical drawing of a generic board that indicates these areas of reduced clearance and what the available clearance in those areas is.

# The Problem
After changing the locations and number of the screws/pillars, those reduced clearances have changed, along with locations of the boards where that clearance is reduced. So, for now, the drawing is wrong.

# Proposed Solution
Change the drawing. (It's probably way more trouble than it's worth to try and reference this stuff directly from the assembly. It's probably best to just manually change it and hope we don't need to change it again.)

# Criteria for Closing
The drawing must indicate the correct areas/clearances/locations.

Closed 2018-03-05.

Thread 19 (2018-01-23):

Solar tab "slots" can't be covered/touched by structure. Also, change in hole locations.

andrewgreenberg, 2018-01-23:
The 4 narrow (~ 1 mm) vertical slots in the Solar module PCB is where the tabs from the solar modules come through from the front side of the board, get folded 90 degrees, and then get soldered to the PCB at the square footprints located by each slot. The tabs are relatively thick (~ 0.2 mm) tinned copper strips. As currently drawn in:

https://github.com/oresat/oresat-structure/blob/master/Solar/Solar_board_drawing.PDF

The structure "keep out" area partially covers the slots. It can't do that. Only the bare PCB surface is allowed to touch the PCB. My only suggestion is to make the struts on top and bottom thinner so that they avoid the tab slots altogether by some margin (e.g. ~ 0.5 mm).

Finally, the fastener holes in the solar modules aren't centered in the structure's width... should we do that?

Joedang, 2018-01-31:
The aforementioned slots now have (IIRC) 0.25 mm and 0.75 mm clearances around them on the peripheral and inner ends, respectively. The screw holes are now symmetric under reflection around a Z plane on the center of the board's outline.

Closed 2018-01-31.

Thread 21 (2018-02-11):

Move backplane mounting holes off of the solar panel mounting holes

andrewgreenberg, 2018-02-11:
We're moving them into separate holes so it's easier to bolt together, we don't have to have very short screws, and we won't have little air pockets between the bolts.

Joedang, 2018-02-13:
Done. The backplane mounting holes now appear between the solar board mounting holes, and the stand-off holes are on the next strut intersection over from the solar board holes. (This will show up after #23 is closed and I merge from `dev_joe`.)

Someone is going to get really good at tapping small holes...

Closed 2018-02-13.

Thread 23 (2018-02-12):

Update backplane with new 26 pin connector

andrewgreenberg, 2018-02-12:
Replace the 40 pin SMT Har-Flex connector with the new 26 pin through-hole connector, and move it from the "right" of the backplane board to the center of the board. The new connector is the Harting 1521026X4XXXXX. This makes us very sad because we can use any thing less than 38 pins, but the jerks only make he 26 pin version. STEP file can be found [here](https://b2b.harting.com/ebusiness/en_us/itemdocument/15210262401000/STEP).

Joedang, 2018-03-05:
Nope, we're using the 40 pin Tiger Eye connector mentioned in #24.

Closed 2018-03-05.

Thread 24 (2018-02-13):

Pick the actual damn connector

andrewgreenberg, 2018-02-13:
Choose a new connector that is < 29.5 mm wide and has all of the good properties.

Joedang, 2018-03-05:
We're using the Tiger Eye TFM_120_01_L_D_RA and SFM_120_01_L_D_LC. They're close to that 29.5 mm size that's dictated by the screws that stabilize the backplane. However, they're always offset from the center of the screws, so it's NBD.

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

Closed 2018-03-05.

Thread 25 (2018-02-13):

Rename all the things

Joedang, 2018-02-13:
A bunch of the names of things don't really follow the naming convention in the [contribution guide](https://github.com/oresat/oresat-structure/blob/master/.github/CONTRIBUTING.md) or aren't really clear. They should be renamed.

## Things with names that should be changed
- [ ] doc/CubesatDesignSpec.pdf -> kill
- [ ] drawings -> merge into appropriate directories
- [ ] hardware -> merge into COTS
- [ ] head-tail -> Zneg_endcard and Zpos_endcap
- [ ] Zneg -> Zneg_endcap
- [ ] Zpos -> Zpos_endcap
- [ ] inhibit -> InhibitCard
- [ ] keepout -> volumeKeepout
- [ ] rack -> frames
- [ ] CardModules -> Camera

When done, open the top level assembly, point it to the new locations, save everything, and push the updated references. (Also, inform people that there are going to be a bunch of changes to both locations and CAD files.)

andrewgreenberg, 2019-04-29:
All the things were renamed! So much way better.

Closed 2019-04-29.

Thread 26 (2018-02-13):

Fix solar connector and verify PCB against DXF

andrewgreenberg, 2018-02-13:
In the current CAD, the Alta 5 cell module has four slots the tabs go through. The top two slots are underneath the Aluminum frame, so I shifted the entire module down (slots and all) by 0.5 mm.

Please update the CAD and drawings of the solar panels.

andrewgreenberg, 2018-08-05:
Joe: Can you please verify this?

andrewgreenberg, 2018-08-05:
Probably done, but we should really verify this.

andrewgreenberg, 2018-10-07:
OK ignore all the stuff above: The solar connectors are wrong. Change to the through hole versions, and then verify the PCB outlines and BSTOP layers against the new DXF from Jeremy.

jalouke, 2018-10-07:
The drawing is updated to include the center location of the connector. The change is on the "footprints" page.

andrewgreenberg, 2019-04-29:
Done!

Closed 2019-04-29.

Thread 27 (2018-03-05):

Place the Tiger Eye connectors on the backplane

Joedang, 2018-03-05:
Place the new connectors, add holes to the backplane for their harpoon thingies, remove the old holes, and update the drawing

# Background
We switched to a different kind of standard connector. See #24.

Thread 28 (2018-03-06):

Add +X frame "hold downs" to the keep outs areas of the drawings for the Generic OreSat Card .

andrewgreenberg, 2018-03-06:
We added struts across the +x frame to hold down the many OreSat cards we have. Please put the keepouts in the OreSat Generic Card drawing so we don't place components in them.

Joedang, 2018-08-05:
This got put in with the spring pins.

Closed 2018-08-05.

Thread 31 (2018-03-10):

Revise Frame Drawings

Joedang, 2018-03-10:
The +/-X frame drawings are missing the Z width of screw pillars. The drawings should also be distributed over multiple pages (US Letter size), because they're kind of hard to read right now.

Joedang, 2018-08-05:
At this point, the drawings should probably just be redone from scratch. I don't think the originals had anything to do with the lattice on the outside. They certainly don't include the stuff for the spring pins or backplane standoffs.

While we're at it, we should add a statement of which license we're using.

andrewgreenberg, 2019-04-29:
They were redone, closing this old issue.

Closed 2019-04-29.

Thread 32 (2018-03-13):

Add 20 pin auxiliary OreSat connector to the card and backplane

andrewgreenberg, 2018-03-13:
Just to the "left" of the main 40 pin connector, we have room between the fastener cutouts on the OreSat cards to fit a 10 pin auxiliary connector. Please add:

- The [Samtec TFM-110-01-L-D-RA](https://www.digikey.com/products/en?keywords=TFM-110-01-L-D-RA) (here's the [CAD](https://www.samtec.com/partnumber/tfm-110-01-l-d-ra?vendor=digikey)) male right angle connector to the card, centered between far left fastener cutouts.
- The [Samtec SFM-110-01-L-D-LC](https://www.digikey.com/product-detail/en/samtec-inc/SFM-110-01-L-D-LC/SFM-110-01-L-D-LC-ND/7815565) ([CAD](https://www.samtec.com/partnumber/sfm-110-01-l-d-lc?vendor=digikey)) to the backplane.

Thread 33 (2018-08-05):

Extract antenna capstone files and put them in the main assembly

andrewgreenberg, 2018-08-05:
Do what the title says, man, and no satellites catch on fire. Once this is done, move on to end card/end cap issue (Issue #34).

calvin-young, 2018-10-10:
CAD extracted and integrated to assembly.  Just imported STEP files though, so don't expect any nice features.  I can rebuild them if anyone cares.

Closed 2018-10-10.

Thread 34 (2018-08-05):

First CAD for End Cards and End Caps

andrewgreenberg, 2018-08-05:
This is blocked on extracting the antenna capstone CAD (issue #33). Once that's done, we need four more steps:

1. Take a first pass at the +Z end card with the helical deployer. Probably needs fasteners and other "things", including solar connectors.
2. Take a first pass at the -Z end card with the turnstile deployer. Probably needs fasteners and other "things", including solar connectors.
3. Take a first pass at the +Z End cap; it has to let the helical antenna deploy without catching. Post drawing so we can make a prototype cap.
4. Take a first pass at the -Z end cap; it has to let the turnstile antenna deploy without catching. Post drawing so we can make a prototype cap.

calvin-young, 2018-10-10:
First-pass CAD for the antennas is in the assembly.  I will continue to update the helical CAD while John (and/or whoever else is assigned) will be in charge of the turnstile.

andrewgreenberg, 2019-04-29:
Old.

Closed 2019-04-29.

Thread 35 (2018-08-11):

Research adhesives and epoxies

Joedang, 2018-08-11:
Collect information on different adhesives and epoxies. We care about ease/safety of application, outgassing, thermal/electrical conductivity, bond strength/compatibility, elastic modulus, working temperature, and typical applications. We have a few different use cases to fill.

We are going to thermal-epoxy the solar panels to their boards and the boards to the structure. So, we need something with high thermal conductivity. It should probably also have a low elastic modulus and high bond strength with gold and aluminum. It's probably going to experience a fair amount of thermal strain, and we don't want it to crack.

Each card is probably going to get a silastic coating.

We were originally planning on using Locktite for fasteners, but apparently nitronic locking helicoils are sufficient.

We also probably need a general-purpose epoxy for large components and connections.

Epibond 123 and Locktite were suggested. Space-rated epoxy is a thing.

jalouke, 2018-08-11:
Have you looked into using the Torr Seal I sent Andrew last year? It is
meant to be a low off gassing epoxy for high vacuum applications. I may
have more that is getting ready to "expire" soon.

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

Closed 2020-10-18.

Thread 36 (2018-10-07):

Update End Cards with new card design

andrewgreenberg, 2018-10-07:
Take the current prototype card design with the new SMPM connectors, no spring pins, and other changes we've done and bring the +Z and -Z end cards up to date. Export DXFs for connector placement, and then assign this to Andrew so he can actually make up end cards!

Note: be careful of the antenna assemblies (both helical and turnstile), which also sits on the end cards.

andrewgreenberg, 2019-04-29:
Done.

Closed 2019-04-29.

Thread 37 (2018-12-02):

Card notches don't line up with backplane screws

Joedang, 2018-12-02:
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

The backplane has a bunch of screws that hold it to the -X frame. Correspondingly, the cards have notches to avoid hitting these screws. Currently, those notches are not misaligned with the screws. It's not enough to break things, but they should be lined up.

andrewgreenberg, 2019-04-29:
Already fixed!

Closed 2019-04-29.

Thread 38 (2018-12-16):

Deepen the spring pin holes on the ends of the rails

Joedang, 2018-12-16:
With the presently specified hole depths, the spring pins on the -Z ends of the rails don't sit deep enough. When machined, there was some significant variation in how deep the threads/holes went. So, the threaded case of the spring pin sits out too far. Just deepen the holes and extend that chunk of aluminum to make sure it doesn't break through. (Actually, should we be venting that hole?)

IanZabel, 2018-12-19:
I would personally only recommend venting the hole if it is a press fit or excessively deep (like one order-of-magnitude greater than diameter). This one may not warrant it.

andrewgreenberg, 2019-04-29:
This was just done. Don't need to vent, because the spring pins themselves have a hollow core which allows them to vent.

Closed 2019-04-29.

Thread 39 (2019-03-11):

All cards needs some tolerance gap on the +/-Y faces of the +X end of the cards.

andrewgreenberg, 2019-03-11:
When putting on the +X frame with cards in the structure, the cards actually jam into the +X frame. There needs to be some added tolerance in card design so they don't get pinched in the +X frame (tolerance in the +/-Y axis on the +x end of the cards).

andrewgreenberg, 2019-04-29:
Old issue, closing

Closed 2019-04-29.

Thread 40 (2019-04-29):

Wedges and triangles need clearance to fit in their slots

andrewgreenberg, 2019-04-29:
All wedges and triangle wedges need to actually be able to fit in their "snug little homes", i.e. their slots. Make sure there's enough tolerance in their width to be able to fit. We usually give 0.1 mm (~ 4 mils) of clearance.

Finally, please check for other clearance problems, including in the corners where machining might requires radii on the internal corners.

Closed 2019-09-25.

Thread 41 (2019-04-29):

Holes for the frame's M2.5 socket head bolts to be fixed

andrewgreenberg, 2019-04-29:
The counterbored holes in the +/-X frames  for the M2.5 socket head bolts is current countersunk. Change to counter board, and bring the head of the bolt towards the surface of the rail in order to add more material under the head - it's unnecessarily tight under the head.

This will also require those M2.5 bolts to get longer.

catiespivey, 2019-04-29:
reduced head clearance by 2mm and changed screw length from 8mm to 10mm and updated the drawings to reflect this change

Closed 2019-04-29.

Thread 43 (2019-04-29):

Update backplane: new connectors for End Cards and small slot widths

andrewgreenberg, 2019-04-29:
The backplane CAD needs to be updated:

- The end cards (location #1 and #20) now use the 40 pin connector.
- Add 0.1 mm clearance on both sides of the backplane so it doesn't hit the -X frame.
- Reduce the size of the slot widths on the top and bottom solar panel cutouts from a diameter of 2.54 mm to 1 mm. Please add the "extra" room towards the end card connector, so we can -route wires near the connectors.

andrewgreenberg, 2019-05-13:
The holes in the backplane for the M2 screws are 2.2 mm. This is a "tight" clearance. 2. mm is "standard clearance, and 2.6 is "loose". Because the top/bottom shoulder bolts do the aligning of the board, the M2s just keep the board against the -X frame. So I'm making those holes 2.6 mm in diameter; please put note that in the backplane drawing. Thanks!

Closed 2019-09-25.

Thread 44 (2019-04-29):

Integrate battery the battery assembly into the main assembly

andrewgreenberg, 2019-04-29:
Not sure where the status of the battery board assembly is - please integrate it into the main assembly. Also, bonus points for adding bother battery boards into the main assembly so that we can start to really see card slot usage.

Closed 2019-09-25.

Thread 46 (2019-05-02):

Match +/-Y frame tabs with +X tabs, move top and bottom tabs

andrewgreenberg, 2019-05-02:
While working with Oleg on placing the battery cards, we realized that the "tabs" on the +/-Y frames (the tabs that have the M2.5 helicoils in them) are too large in the Z axis. They scrape the cards that are above and below them. The tabs on the +X frame seems to be sized correctly, so you could just match that. There are 8 tabs all together, and I think doing this on the "inner" 4 tabs will work.

There's an issue for the outer four tabs, however: they also have alignment pins in them. I think it might work if we move these outer tabs to just below the end caps - if we did that, they could touch the end caps, and thus have room for the pins. The sides that touch the end cards, however, still do need to be cut back.

This all probably needs a drawing, so let's chat on Thu/Fri. It also might be weirdly complicated, so I'm CC'ing Ryan on this one.

catiespivey, 2019-09-25:
I think this is a non issue now?

Closed 2019-09-25.

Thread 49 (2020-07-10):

OreSat0 Assembly not correctly aligned with axes

EmilioGizzi, 2020-07-10:
OreSat0's X axis is in the wrong direction, and the Y and Z are swapped.

Closed 2020-07-12.

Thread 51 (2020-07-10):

OreSat0 Backplane PCB needs to be redone.

EmilioGizzi, 2020-07-10:
To quickly calculate the mass of the satellite, I cut OreSat1's backplane in half and stuck it in. We need to properly make an actual backplane for OreSat0 in the same way that OreSat1's was made.

Closed 2020-07-12.

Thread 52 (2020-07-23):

OreSat 1 is missing inhibit switch cutouts.

EmilioGizzi, 2020-07-23:
Add inhibit switch cutouts with the same dimensions as the ones in OreSat0

Closed 2020-08-20.

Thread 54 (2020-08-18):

Widen Y frame dowel holes - they're just too tight.

andrewgreenberg, 2020-08-18:

Closed 2020-10-18.

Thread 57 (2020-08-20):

Remove backplane connectors 7 and 8 from the assembly (they interfere with the battery)

andrewgreenberg, 2020-08-20:
Write a short (single sentence) description of the problem to someone already familiar with the project.

# Background
Provide some relevant information on the decisions that led up to this problem and how stuff works.
Someone who reads the background should be able to understand your short description.
6 months from now, you should be able to remember what this issue was about by reading the short description, without looking at the background.

# The Problem
Describe at length what needs to be changed and why what we have now is not what we want.
Remeber to provide relevant screenshots, pictures, minimum working examples, and/or error messages.

# Proposed Solution
Describe how this problem might be solved.
Remeber to tag people who may have the skills, knowledge, or motivation to solve the problem.

# Criteria for Closing
Describe what needs to happen for this problem to be considered solved.
Checklists are helpful here.

Closed 2020-08-20.

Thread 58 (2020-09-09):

-Z rail ends have spring pins, but they stick out when screwed in

andrewgreenberg, 2020-09-09:
Add a few more mm of threaded hole depth for the spring pins on the -Z ends... right now, the spring pins bottom out in the hole before they're fully embedded in the rail ends, leaving a CDS-violating "nub" sticking out of the rail. Please measure the spring pins to find out why our 3D model failed, too.

Closed 2020-10-18.

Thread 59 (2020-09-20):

In OreSat0, the star tracker camera is centered in the solar module holes in CAD, but not real life?

andrewgreenberg, 2020-09-20:
Is this a CAD issue, solar module issue, star tracker issue, or... ?

Closed 2020-10-18.

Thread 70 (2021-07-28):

Add an upper, and maybe lower slot, to the RW assembly area to the 1.5U, 2U, and 3U frames

andrewgreenberg, 2021-07-28:
Not everyone will use the RWs/MTs, we should have as many slots there as possible. Certainly add the obvious one at the top of the assembly, but I'm unclear if adding another slot at the bottom (above the ACS card) will screw things up.

marvinlinn, 2021-09-27:
Checked and solution determined that extra slot would not be useful. Instead, reaction wheel-less designs were made.

Closed 2021-09-27.

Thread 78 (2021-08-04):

Fix Battery Inhibit Tolerance Issue

marvinlinn, 2021-08-04:
Inhibit switches currently interfere with the card wedge system--adjust the mating distance to be <0.5mm and/or modify inhibit design for more room.

Closed 2021-08-09.

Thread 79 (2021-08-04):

Interference issues with new reaction control wheel mount design

marvinlinn, 2021-08-04:
After the redesign of the reaction control wheel mount, a few interference issues were present. See images below for issues:

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

marvinlinn, 2021-08-06:
Redesigning the entire magnetorquer design--will resolve interference issues.

Closed 2021-08-08.

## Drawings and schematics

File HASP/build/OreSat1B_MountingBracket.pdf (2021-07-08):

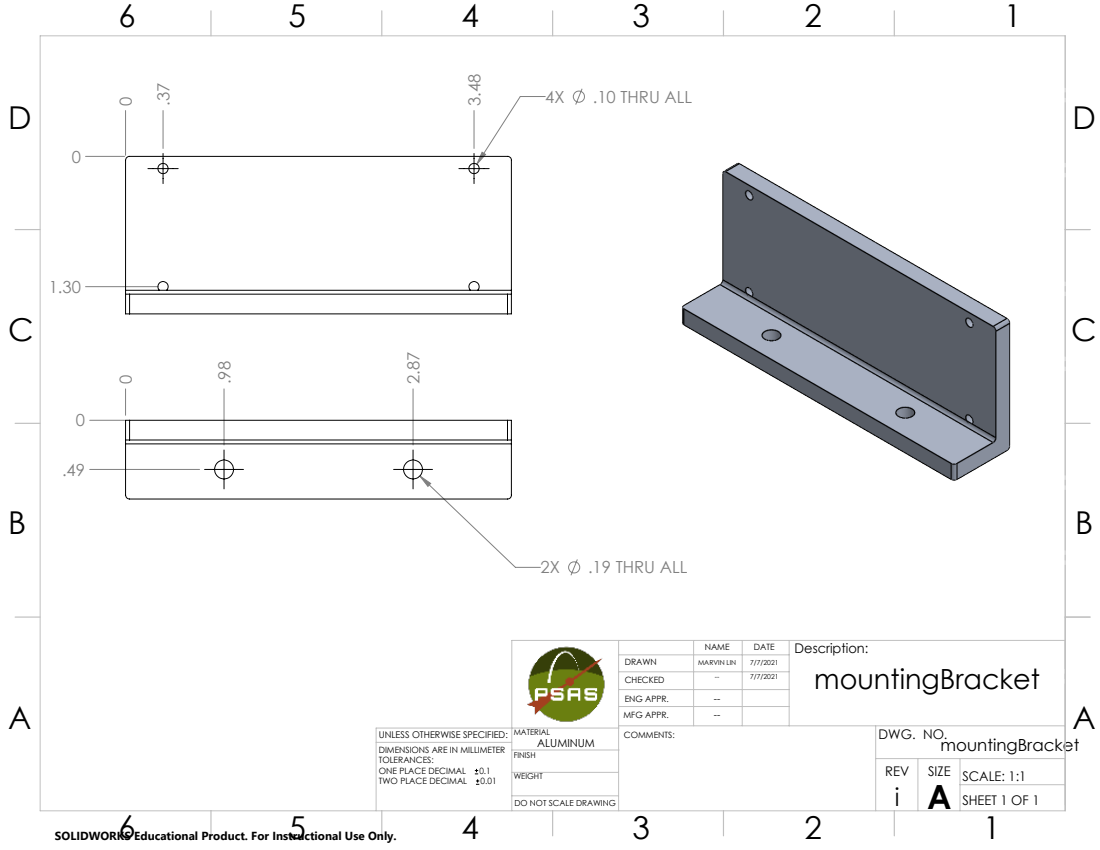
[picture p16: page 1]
.10 THRU ALL; .19 THRU ALL; REV; SCALE: 1:1; DO NOT SCALE DRAWING; SHEET 1 OF 1

NAME | DATE | Description: mountingBracket

DRAWN | MARVIN LIN | 7/7/2021
CHECKED | -- | 7/7/2021
ENG APPR. | --
MFG APPR. | --

UNLESS OTHERWISE SPECIFIED: | MATERIAL ALUMINUM | COMMENTS: | DWG. NO.

DIMENSIONS ARE IN MILLIMETER
TOLERANCES:
ONE PLACE DECIMAL 0.1
TWO PLACE DECIMAL 0.01

SOLIDWORKS Educational Product. For Instructional Use Only.

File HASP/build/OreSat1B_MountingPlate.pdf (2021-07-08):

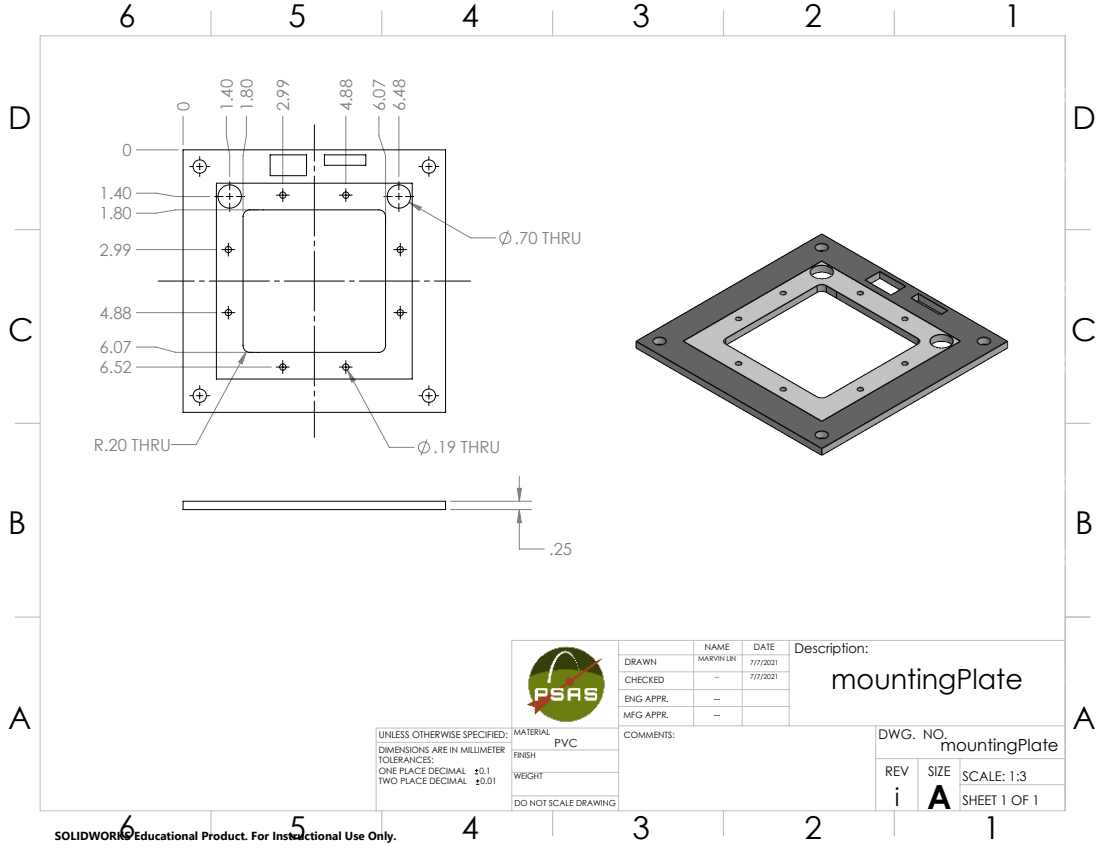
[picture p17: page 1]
R.20 THRU; .19 THRU; .70 THRU; REV; SCALE: 1:3; DO NOT SCALE DRAWING; SHEET 1 OF 1

NAME | DATE | Description: mountingPlate

DRAWN | MARVIN LIN | 7/7/2021
CHECKED | -- | 7/7/2021
ENG APPR. | --
MFG APPR. | --

UNLESS OTHERWISE SPECIFIED: | MATERIAL PVC | COMMENTS: | DWG. NO. mountingPlate

DIMENSIONS ARE IN MILLIMETER
TOLERANCES:
ONE PLACE DECIMAL 0.1
TWO PLACE DECIMAL 0.01

SOLIDWORKS Educational Product. For Instructional Use Only.

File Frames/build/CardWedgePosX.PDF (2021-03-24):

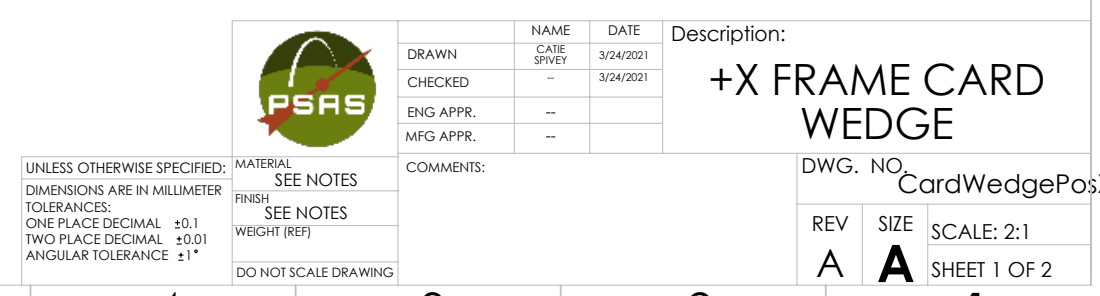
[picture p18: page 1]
REV; SCALE: 2:1; DO NOT SCALE DRAWING; SHEET 1 OF 2; WEIGHT (REF); SEE NOTES

REVISIONS

ZONE | REV. | DESCRIPTION | DATE | APPROVED

A | INITIAL RELEASE | 9/4/2019

NAME | DATE | Description: +X FRAME CARD WEDGE

DRAWN | CATIE SPIVEY | 3/24/2021
CHECKED | -- | 3/24/2021
ENG APPR. | --
MFG APPR. | --

UNLESS OTHERWISE SPECIFIED: | MATERIAL SEE NOTES | COMMENTS: | DWG. NO.

DIMENSIONS ARE IN MILLIMETER
TOLERANCES:
ONE PLACE DECIMAL 0.1
TWO PLACE DECIMAL 0.01
ANGULAR TOLERANCE 1

SOLIDWORKS Educational Product. For Instructional Use Only.

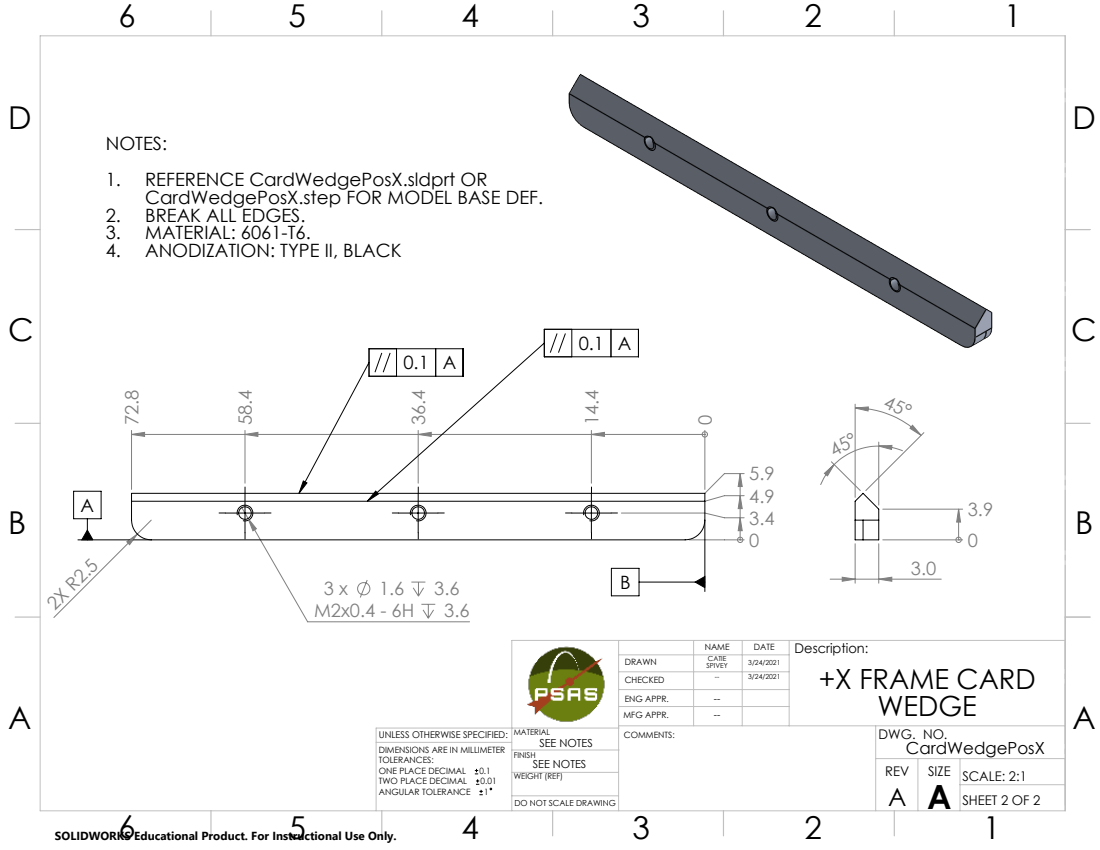
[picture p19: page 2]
REV; SCALE: 2:1; DO NOT SCALE DRAWING; SHEET 2 OF 2; WEIGHT (REF); SEE NOTES

NOTES:
1. REFERENCE CardWedgePosX.sldprt OR
CardWedgePosX.step FOR MODEL BASE DEF.
2. BREAK ALL EDGES.
3. MATERIAL: 6061-T6.
4. ANODIZATION: TYPE II, BLACK

NAME | DATE | Description: +X FRAME CARD WEDGE

DRAWN | CATIE SPIVEY | 3/24/2021
CHECKED | -- | 3/24/2021
ENG APPR. | --
MFG APPR. | --

UNLESS OTHERWISE SPECIFIED: | MATERIAL SEE NOTES | COMMENTS: | DWG. NO. CardWedgePosX

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

SOLIDWORKS Educational Product. For Instructional Use Only.

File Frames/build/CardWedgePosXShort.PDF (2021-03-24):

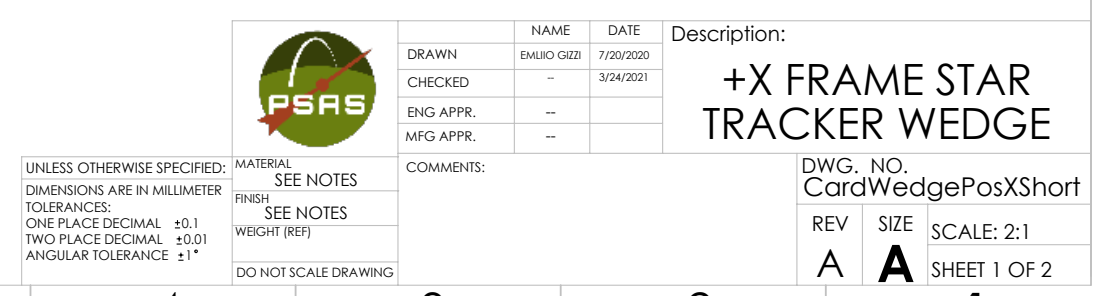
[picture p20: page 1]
REV; SCALE: 2:1; DO NOT SCALE DRAWING; SHEET 1 OF 2; WEIGHT (REF); SEE NOTES

REVISIONS

ZONE | REV. | DESCRIPTION | DATE | APPROVED

A | INITIAL RELEASE | 7/20/2020

NAME | DATE | Description: +X FRAME STAR TRACKER WEDGE

DRAWN | EMLIIO GIZZI | 7/20/2020
CHECKED | -- | 3/24/2021
ENG APPR. | --
MFG APPR. | --

UNLESS OTHERWISE SPECIFIED: | MATERIAL SEE NOTES | COMMENTS: | DWG. NO. CardWedgePosXShort

DIMENSIONS ARE IN MILLIMETER
TOLERANCES:
ONE PLACE DECIMAL 0.1
TWO PLACE DECIMAL 0.01
ANGULAR TOLERANCE 1

SOLIDWORKS Educational Product. For Instructional Use Only.

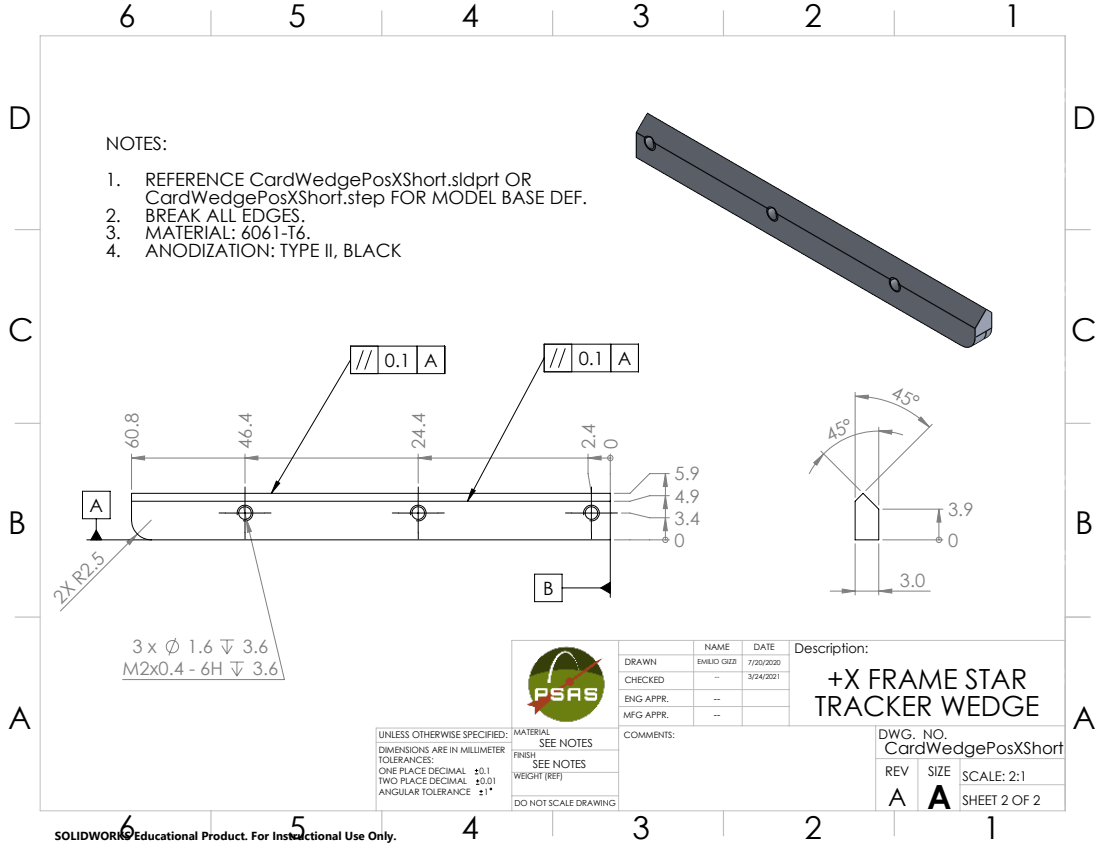
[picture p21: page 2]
REV; SCALE: 2:1; DO NOT SCALE DRAWING; SHEET 2 OF 2; WEIGHT (REF); SEE NOTES

NOTES:
1. REFERENCE CardWedgePosXShort.sldprt OR
CardWedgePosXShort.step FOR MODEL BASE DEF.
2. BREAK ALL EDGES.
3. MATERIAL: 6061-T6.
4. ANODIZATION: TYPE II, BLACK

NAME | DATE | Description: +X FRAME STAR TRACKER WEDGE

DRAWN | EMILIO GIZZI | 7/20/2020
CHECKED | -- | 3/24/2021
ENG APPR. | --
MFG APPR. | --

UNLESS OTHERWISE SPECIFIED: | MATERIAL SEE NOTES | COMMENTS: | DWG. NO. CardWedgePosXShort

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

SOLIDWORKS Educational Product. For Instructional Use Only.

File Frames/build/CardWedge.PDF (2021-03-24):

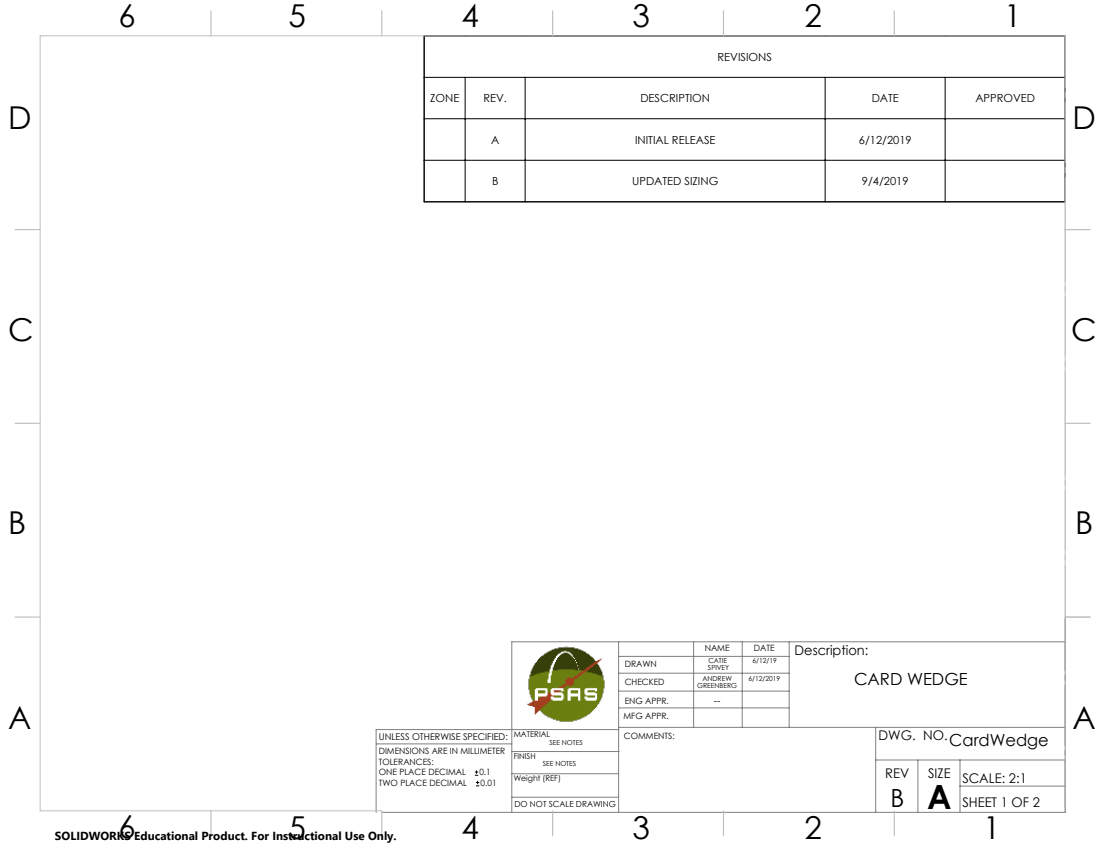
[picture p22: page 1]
Weight (REF); SEE NOTES; SHEET 1 OF 2; SCALE: 2:1

REVISIONS

ZONE | REV. | DESCRIPTION | DATE | APPROVED

A | INITIAL RELEASE | 6/12/2019

B | UPDATED SIZING | 9/4/2019

DATE | Description: NAME CARD WEDGE
DRAWN | CATIE SPIVEY | 6/12/19
CHECKED | ANDREW GREENBERG | 6/12/2019

ENG APPR. | --
MFG APPR.

UNLESS OTHERWISE SPECIFIED: | MATERIAL SEE NOTES | COMMENTS: | DWG. NO. CardWedge

DIMENSIONS ARE IN MILLIMETER
TOLERANCES:
ONE PLACE DECIMAL 0.1
TWO PLACE DECIMAL 0.01

DO NOT SCALE DRAWING

SOLIDWORKS Educational Product. For Instructional Use Only.

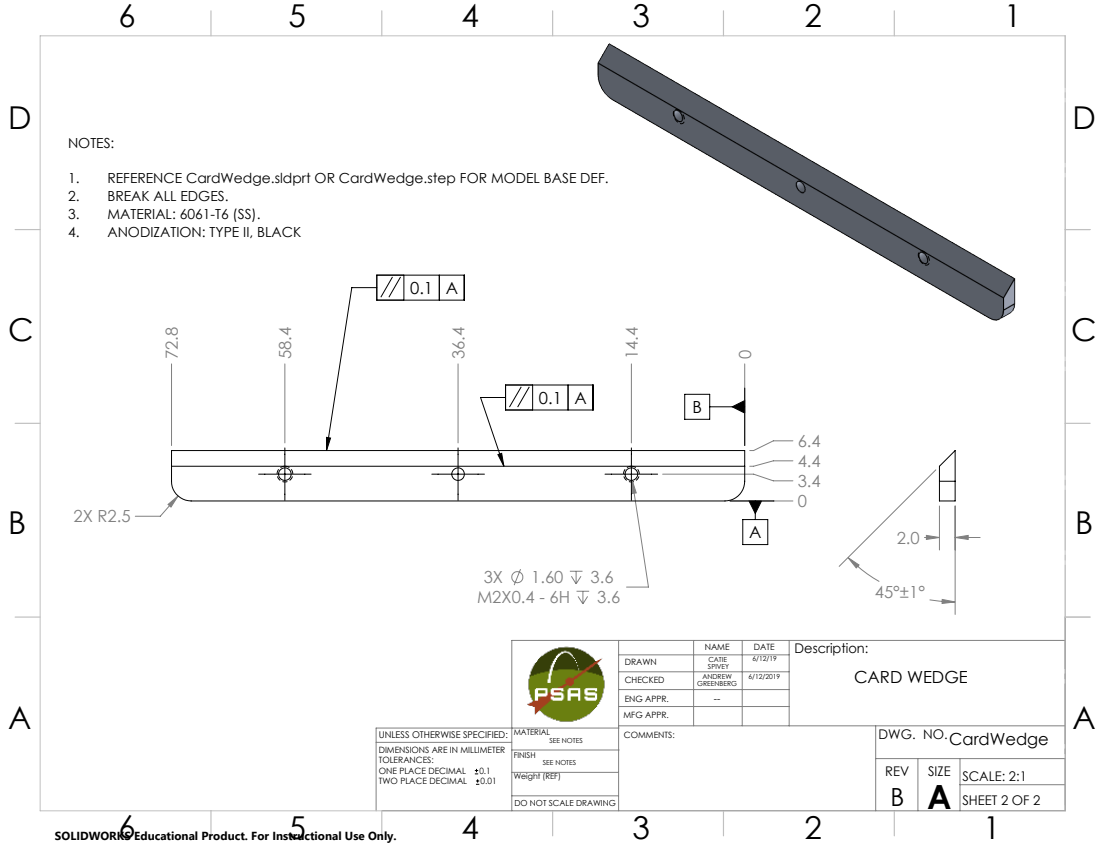
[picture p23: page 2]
Weight (REF); SEE NOTES; SHEET 2 OF 2; SCALE: 2:1

1. REFERENCE CardWedge.sldprt OR CardWedge.step FOR MODEL BASE DEF.
2. BREAK ALL EDGES.
3. MATERIAL: 6061-T6 (SS).
4. ANODIZATION: TYPE II, BLACK

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

ENG APPR. | --
MFG APPR.

UNLESS OTHERWISE SPECIFIED: | MATERIAL SEE NOTES | COMMENTS: | DWG. NO. CardWedge

DIMENSIONS ARE IN MILLIMETER
TOLERANCES:
ONE PLACE DECIMAL 0.1
TWO PLACE DECIMAL 0.01

DO NOT SCALE DRAWING

SOLIDWORKS Educational Product. For Instructional Use Only.

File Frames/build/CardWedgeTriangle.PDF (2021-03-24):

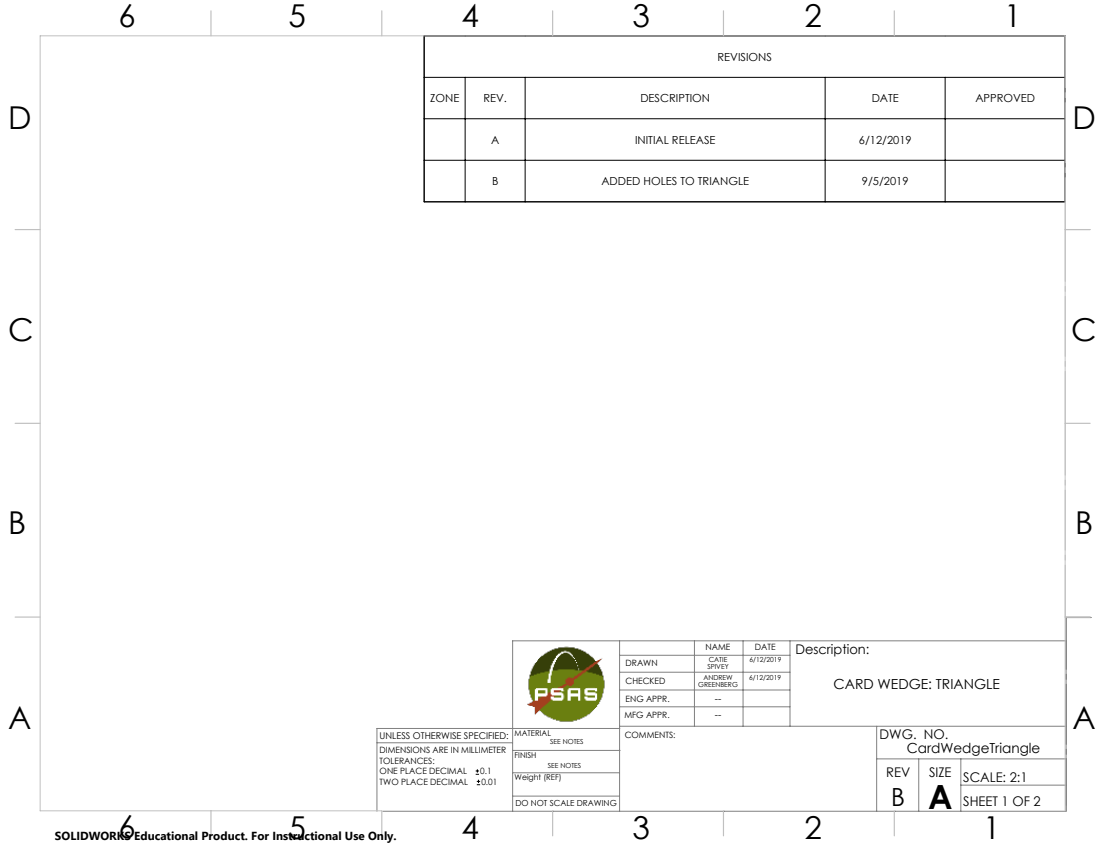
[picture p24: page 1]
Weight (REF); SEE NOTES; SHEET 1 OF 2; SCALE: 2:1

REVISIONS

ZONE | REV. | DESCRIPTION | DATE | APPROVED

A | INITIAL RELEASE | 6/12/2019

B | ADDED HOLES TO TRIANGLE | 9/5/2019

DATE | Description: NAME CARD WEDGE: TRIANGLE

DRAWN | CATIE SPIVEY | 6/12/2019
CHECKED | ANDREW GREENBERG | 6/12/2019
ENG APPR. | --
MFG APPR. | --

UNLESS OTHERWISE SPECIFIED: | MATERIAL SEE NOTES | COMMENTS: | DWG. NO. CardWedgeTriangle

DIMENSIONS ARE IN MILLIMETER
TOLERANCES:
ONE PLACE DECIMAL 0.1
TWO PLACE DECIMAL 0.01

DO NOT SCALE DRAWING

SOLIDWORKS Educational Product. For Instructional Use Only.

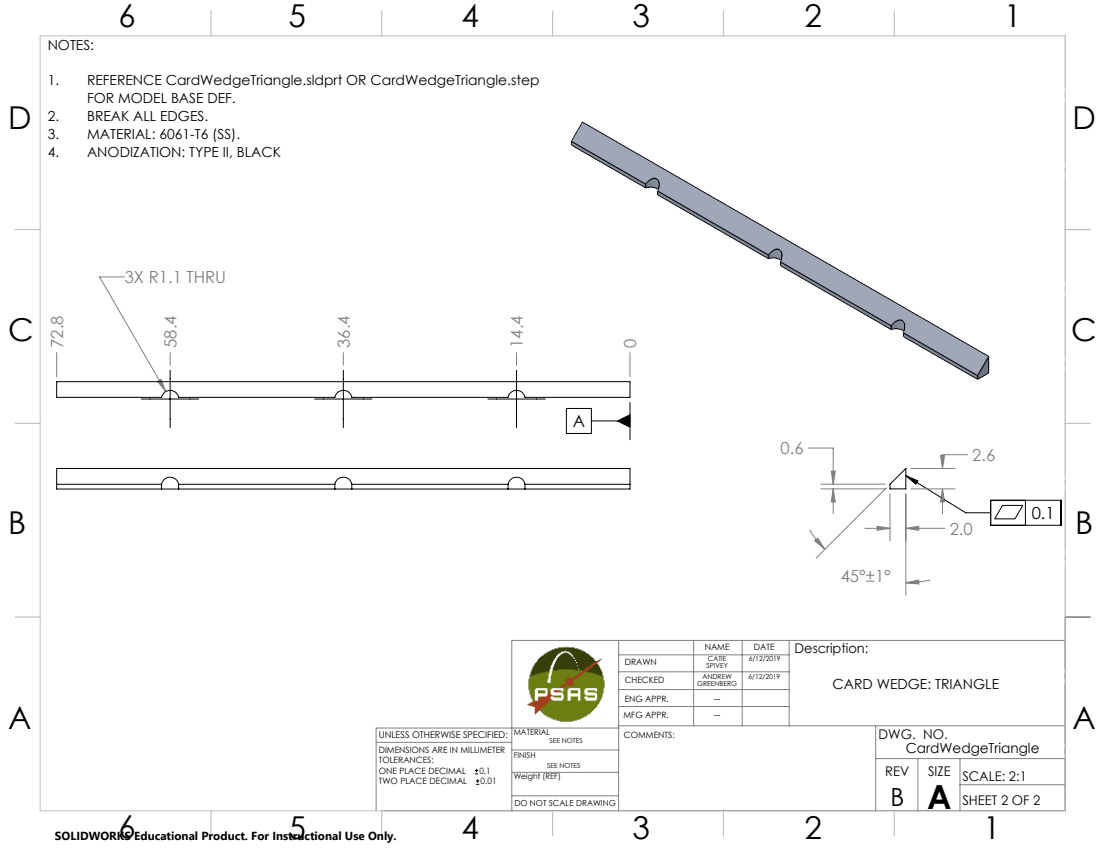
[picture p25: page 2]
Weight (REF); SEE NOTES; SHEET 2 OF 2; SCALE: 2:1; 3X R1.1 THRU

NOTES:
2. BREAK ALL EDGES.
3. MATERIAL: 6061-T6 (SS).
4. ANODIZATION: TYPE II, BLACK

1. REFERENCE CardWedgeTriangle.sldprt OR CardWedgeTriangle.step
FOR MODEL BASE DEF.

DATE | Description: NAME CARD WEDGE: TRIANGLE

DRAWN | CATIE SPIVEY | 6/12/2019
CHECKED | ANDREW GREENBERG | 6/12/2019
ENG APPR. | --
MFG APPR. | --

UNLESS OTHERWISE SPECIFIED: | MATERIAL SEE NOTES | COMMENTS: | DWG. NO. CardWedgeTriangle

DIMENSIONS ARE IN MILLIMETER
TOLERANCES:
ONE PLACE DECIMAL 0.1
TWO PLACE DECIMAL 0.01

DO NOT SCALE DRAWING

SOLIDWORKS Educational Product. For Instructional Use Only.

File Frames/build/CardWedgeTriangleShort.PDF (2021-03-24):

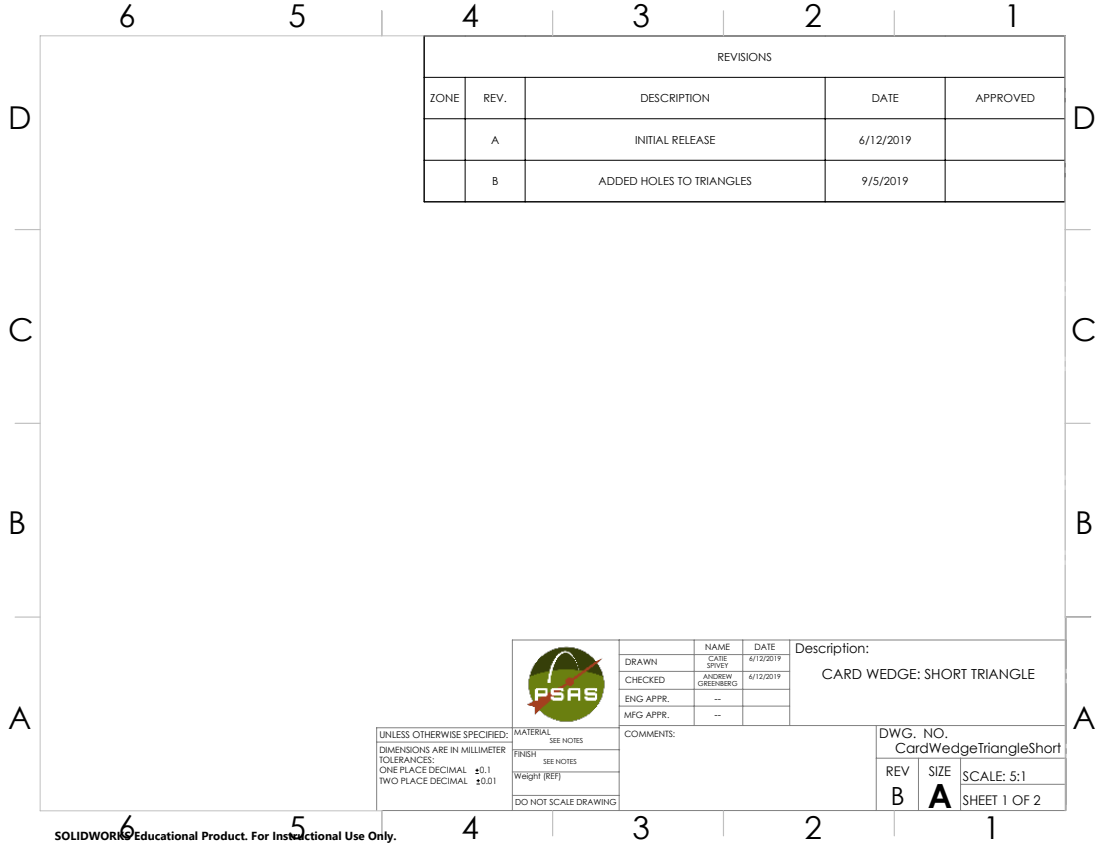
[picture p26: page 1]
Weight (REF); SEE NOTES; SHEET 1 OF 2; SCALE: 5:1

REVISIONS

ZONE | REV. | DESCRIPTION | DATE | APPROVED

A | INITIAL RELEASE | 6/12/2019

B | ADDED HOLES TO TRIANGLES | 9/5/2019

DATE | Description: NAME CARD WEDGE: SHORT TRIANGLE

DRAWN | CATIE SPIVEY | 6/12/2019
CHECKED | ANDREW GREENBERG | 6/12/2019
ENG APPR. | --
MFG APPR. | --

UNLESS OTHERWISE SPECIFIED: | MATERIAL SEE NOTES | COMMENTS: | DWG. NO. CardWedgeTriangleShort

DIMENSIONS ARE IN MILLIMETER
TOLERANCES:
ONE PLACE DECIMAL 0.1
TWO PLACE DECIMAL 0.01

DO NOT SCALE DRAWING

SOLIDWORKS Educational Product. For Instructional Use Only.

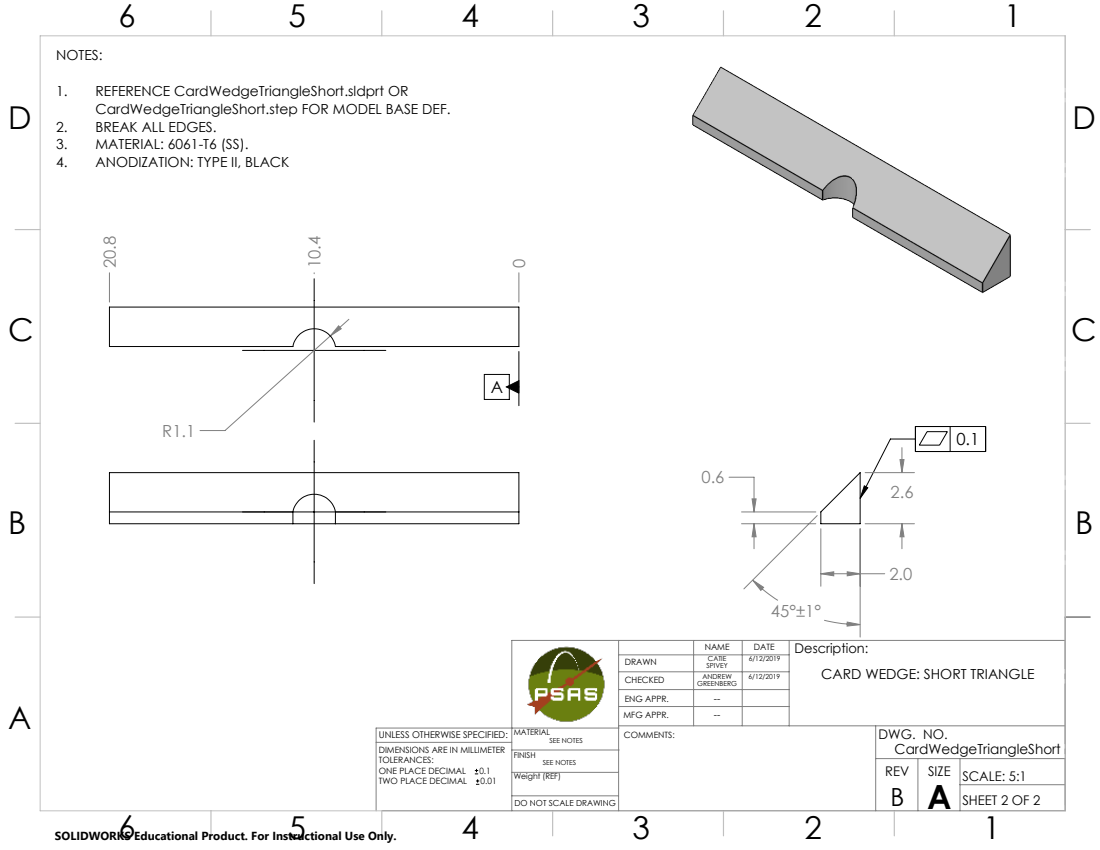
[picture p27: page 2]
Weight (REF); SEE NOTES; SHEET 2 OF 2; SCALE: 5:1

NOTES:
2. BREAK ALL EDGES.
3. MATERIAL: 6061-T6 (SS).
4. ANODIZATION: TYPE II, BLACK

1. REFERENCE CardWedgeTriangleShort.sldprt OR
CardWedgeTriangleShort.step FOR MODEL BASE DEF.

DATE | Description: NAME CARD WEDGE: SHORT TRIANGLE

DRAWN | CATIE SPIVEY | 6/12/2019
CHECKED | ANDREW GREENBERG | 6/12/2019
ENG APPR. | --
MFG APPR. | --

UNLESS OTHERWISE SPECIFIED: | MATERIAL SEE NOTES | COMMENTS: | DWG. NO. CardWedgeTriangleShort

DIMENSIONS ARE IN MILLIMETER
TOLERANCES:
ONE PLACE DECIMAL 0.1
TWO PLACE DECIMAL 0.01

DO NOT SCALE DRAWING

SOLIDWORKS Educational Product. For Instructional Use Only.

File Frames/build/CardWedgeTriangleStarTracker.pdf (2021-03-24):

REV; SCALE: 1:1; DO NOT SCALE DRAWING; SHEET 1 OF 2

REVISIONS

ZONE | REV. | DESCRIPTION | DATE | APPROVED

A | INITIAL RELEASE | 8/19/2020

NAME | DATE | Description: Card Wedge: Star Tracker Triangle

DRAWN | EMILIO GIZZI | 8/19/2020
CHECKED | -- | 3/24/2021
ENG APPR. | --
MFG APPR. | --

UNLESS OTHERWISE SPECIFIED: | MATERIAL SEE NOTES | COMMENTS: | DWG. NO. CardWedgeTriangleStarTracker

DIMENSIONS ARE IN MILLIMETER
TOLERANCES:
ONE PLACE DECIMAL 0.1
TWO PLACE DECIMAL 0.01

SOLIDWORKS Educational Product. For Instructional Use Only.

REV; SCALE: 2:1; DO NOT SCALE DRAWING; SHEET 2 OF 2

1. REFERENCE CardWedgeTriangle.sldprt OR
CardWedgeTriangleStarTracker.step FOR MODEL BASE DEF.
2. BREAK ALL EDGES.
3. MATERIAL: 6061-T6 (SS).
4. ANODIZATION: TYPE II, BLACK

NAME | DATE | Description: Card Wedge: Star Tracker Triangle

DRAWN | EMILIO GIZZI | 8/19/2020
CHECKED | -- | 3/24/2021
ENG APPR. | --
MFG APPR. | --

UNLESS OTHERWISE SPECIFIED: | MATERIAL SEE NOTES | COMMENTS: | DWG. NO. CardWedgeTriangleStarTracker

DIMENSIONS ARE IN MILLIMETER
TOLERANCES:
ONE PLACE DECIMAL 0.1
TWO PLACE DECIMAL 0.01

SOLIDWORKS Educational Product. For Instructional Use Only.

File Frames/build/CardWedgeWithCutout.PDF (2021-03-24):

SHEET 1 OF 2; SCALE: 2:1

REVISIONS

ZONE | REV. | DESCRIPTION | DATE | APPROVED

A | INITIAL RELEASE | 6/12/2019

NAME | DATE | Description: CARD WEDGE WITH CUTOUT

DRAWN | CATIE SPIVEY | 6/12/2019
CHECKED | ANDREW GREENBERG | 6/12/2019
ENG APPR. | --
MFG APPR. | --

UNLESS OTHERWISE SPECIFIED: | MATERIAL 6061-T6 (SS) | COMMENTS: | DWG. NO. CardWedgeWithCutout

DIMENSIONS ARE IN MILLIMETER
TOLERANCES:
ONE PLACE DECIMAL 0.1
TWO PLACE DECIMAL 0.01

FINISH
ANODIZATION TYPE II -BLACK
Weight (REF)

DO NOT SCALE DRAWING

SOLIDWORKS Educational Product. For Instructional Use Only.

SHEET 2 OF 2; SCALE: 2:1; M2x0.4 Tapped Hole

NOTES:
2. BREAK ALL EDGES.
3. MATERIAL: 6061-T6 (SS).
4. ANODIZATION: TYPE II, BLACK

1. REFERENCE CardWedgeWithCutout.sldprt OR CardWedgeWithCutout.step
FOR MODEL BASE DEF.

NAME | DATE | Description: CARD WEDGE WITH CUTOUT

DRAWN | CATIE SPIVEY | 6/12/2019
CHECKED | ANDREW GREENBERG | 6/12/2019
ENG APPR. | --
MFG APPR. | --

UNLESS OTHERWISE SPECIFIED: | MATERIAL 6061-T6 (SS) | COMMENTS: | DWG. NO. CardWedgeWithCutout

DIMENSIONS ARE IN MILLIMETER
TOLERANCES:
ONE PLACE DECIMAL 0.1
TWO PLACE DECIMAL 0.01

FINISH
ANODIZATION TYPE II -BLACK
Weight (REF)

DO NOT SCALE DRAWING

SOLIDWORKS Educational Product. For Instructional Use Only.

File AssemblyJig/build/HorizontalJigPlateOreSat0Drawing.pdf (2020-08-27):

FINISH (REF); REV; SCALE: 1:3; DO NOT SCALE DRAWING; SHEET 1 OF 2; WEIGHT (REF)

REVISIONS

REV. | DESCRIPTION | DATE | INITIALS

A | INITIAL RELEASE | 8/23/2020 | EL

NOTES:
1. REFERENCE HorizontalJigPlateOresat0.sldprt
OR HorizontalJigPlateOresat0.step FOR MODEL BASE DEF
2. BREAK ALL EDGES.
3. MATERIAL: 6061-T6 ALUMINUM

NAME | DATE | Description: HORIZONTAL JIG ORESAT 0

DRAWN | EMMA LEVY | 8/26/2020
CHECKED | CATIE SPIVEY | 8/26/2020
ENG APPR. | --
MFG APPR. | --

UNLESS OTHERWISE SPECIFIED: | MATERIAL 6061-T6 ALUMINUM | COMMENTS: | DWG. NO. HorizontalJigPlateOreSat0Drawing

DIMENSIONS ARE IN MILLIMETER
TOLERANCES:
ONE PLACE DECIMAL 0.1
TWO PLACE DECIMAL 0.05

SOLIDWORKS Educational Product. For Instructional Use Only.

7.62 TYP; 8.74 THRU ALL; R2.00 TYP; 6.35 THRU ALL; FINISH (REF); REV; SCALE: 1:3; DO NOT SCALE DRAWING; SHEET 2 OF 2; WEIGHT (REF)

PART IS SYMMETRIC ABOUT LINES A AND B

NAME | DATE | Description: HORIZONTAL JIG ORESAT 0

DRAWN | EMMA LEVY | 8/26/2020
CHECKED | CATIE SPIVEY | 8/26/2020
ENG APPR. | --
MFG APPR. | --

UNLESS OTHERWISE SPECIFIED: | MATERIAL 6061-T6 ALUMINUM | COMMENTS: | DWG. NO. HorizontalJigPlateOreSat0Drawing

DIMENSIONS ARE IN MILLIMETER
TOLERANCES:
ONE PLACE DECIMAL 0.1
TWO PLACE DECIMAL 0.05

SOLIDWORKS Educational Product. For Instructional Use Only.

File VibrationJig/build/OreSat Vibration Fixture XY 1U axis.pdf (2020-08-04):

FINISH (REF); REV; SCALE: 1:3; DO NOT SCALE DRAWING; SHEET 1 OF 3; Weight (REF)

REVISIONS

ZONE | REV. | DESCRIPTION | DATE | APPROVED

A | INITIAL RELEASE | 7/10/2020

B | TIGHTENED CRITIAL TOLERANCES | 8/4/2020

NAME | DATE | Description: VIBRATION FIXTURE HORIZONTAL

DRAWN | E. ISAACS | 7/10/2020
CHECKED | EMILIO GIZZI | 8/4/2020
ENG APPR. | --
MFG APPR. | --

UNLESS OTHERWISE SPECIFIED: | MATERIAL DELRIN | COMMENTS: | DWG. NO. OreSat Vibration Fixture XY 1U axis

DIMENSIONS ARE IN MILLIMETER
TOLERANCES:
ONE PLACE DECIMAL 0.1
TWO PLACE DECIMAL 0.01

SOLIDWORKS Educational Product. For Instructional Use Only.

FINISH (REF); REV; SCALE: 1:3; Weight (REF)

NOTES:
1. REFERENCE OreSat Vibration Fixture XY axis.sldprt OR
OreSat Vibration Fixture XY axis.step FOR MODEL BASE DEF.

2. BREAK ALL EDGES.
3. MATERIAL: DELRIN.

NAME | DATE | Description: VIBRATION FIXTURE HORIZONTAL

DRAWN | E. ISAACS | 7/10/2020
CHECKED | EMILIO GIZZI | 8/4/2020
ENG APPR. | --
MFG APPR. | --

UNLESS OTHERWISE SPECIFIED: | MATERIAL DELRIN | COMMENTS: | DWG. NO. OreSat Vibration Fixture XY 1U axis

DIMENSIONS ARE IN MILLIMETER
TOLERANCES:
ONE PLACE DECIMAL 0.1

12.0 AND 114.0 IS; SECTION A-A; FINISH (REF); REV; SCALE: 1:3; Weight (REF)

NOTE: DISTANCE BETWEEN 12.0
AND 127.5 IS CRITICAL

NAME | DATE | Description: VIBRATION FIXTURE HORIZONTAL

DRAWN | E. ISAACS | 7/10/2020
CHECKED | EMILIO GIZZI | 8/4/2020
ENG APPR. | --
MFG APPR. | --

UNLESS OTHERWISE SPECIFIED: | MATERIAL DELRIN | COMMENTS: | DWG. NO. OreSat Vibration Fixture XY 1U axis

DIMENSIONS ARE IN MILLIMETER
TOLERANCES:
ONE PLACE DECIMAL 0.1

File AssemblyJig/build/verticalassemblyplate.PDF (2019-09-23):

FINISH (REF); REV; SCALE: 1:2; DO NOT SCALE DRAWING; SHEET 1 OF 2; WEIGHT (REF)

NOTES:
1. REFERENCE verticalassemblyplate.sldprt OR
verticalassemblyplate.step FOR MODEL BASE DEF.
2. BREAK ALL EDGES.
3. MATERIAL: ALUMINUM

NAME | DATE | Description: PLATE FOR VERTICAL ASSEMBLY JIG

DRAWN | CATIE SPIVEY | 9/10/2019
CHECKED | -- | 9/10/2019
ENG APPR. | --
MFG APPR. | --

UNLESS OTHERWISE SPECIFIED: | MATERIAL SEE NOTES | COMMENTS: | DWG. NO. verticalassemblyplate

DIMENSIONS ARE IN INCHES
TOLERANCES:
ONE PLACE DECIMAL 0.1
TWO PLACE DECIMAL 0.01

SOLIDWORKS Educational Product. For Instructional Use Only.

R0.08 TYP; 0.30 TYP; 45° TYP; 4.21 TYP; FINISH (REF); REV; SCALE: 1:2; DO NOT SCALE DRAWING; SHEET 2 OF 2; WEIGHT (REF)

NAME | DATE | Description: PLATE FOR VERTICAL ASSEMBLY JIG

DRAWN | CATIE SPIVEY | 9/10/2019
CHECKED | -- | 9/10/2019
ENG APPR. | --
MFG APPR. | --

UNLESS OTHERWISE SPECIFIED: | MATERIAL SEE NOTES | COMMENTS: | DWG. NO. verticalassemblyplate

DIMENSIONS ARE IN INCHES
TOLERANCES:
ONE PLACE DECIMAL 0.1
TWO PLACE DECIMAL 0.01

SOLIDWORKS Educational Product. For Instructional Use Only.

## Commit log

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2017-10-05 started the tail card
    The tail card is the position 19 card that serves as a mezzanine for the
    -Z endcap. It connects to the -Z solar panels with 12 pin connectors, to
    the -Z endcap with a 20 pin and 3 MMCX connectors, and to the backplane
    with a 20 pin and 3 MMCX connectors.
    While messing with the 12 pin connectors, I noticed that the connectors
    for the solar cards are off-center by 0.1 mm (doesn't matter). They're
    also a little misplaced in the Z direction. We'll have to go in and
    tweak their Z position later.
    [12pin_male_rightAngle_1515012X601XXX_100211589MOD000B.SLDPRT, 12pin_male_sraight_1511012X601XXX_100210564MOD000B.SLDPRT, 20pin_male_straight_1511020X601XXX_100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]
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2017-10-06 removed references in board; fixed drawing labels
    I dunno why the drawing labels got the X and Y axes switched. They were
    clearly right at some point, since the PDF shows the right thing.
    [Generic_board.SLDPRT, MODULE_PLACEHOLDER_PCB_WITHRF_2_standardCard.SLDDRW]
2017-10-06 renamed generic board stuff; pointed drawing to it
    Also found some weird labelling problems with the drawing.
    [CARD_GENERIC.SLDASM, Generic_board.SLDDRW, MODULE_PLACEHOLDER_PCB_WITHRF_2_standardCard.SLDDRW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]
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2017-10-06 letting SW touch ALL THE THINGS!
    It really is a problem how it does that...
    [Backplane_1U_Zneg.SLDASM, Camera_card.SLDASM, Generic.SLDASM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]
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2017-12-08 moved rack assembly holes to avoid blind holes
    This isn't done yet (hence the branch). I want to get it so that we
    don't need to worry about correctly-depthed blind holes or about
    accidentally drilling intersecting holes.
    I also want to avoid putting the mounting holes in places that will be
    inconvenient for the head/tail cards.
    [Cuberail_side.SLDPRT]
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2018-01-13 resolved some dimensional inconsistencies
    The screw holes and pillars were misaligned.
    [Cuberail_back.SLDPRT, Cuberail_front.SLDPRT, Cuberail_side.SLDPRT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]
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2018-01-22 fixed side frame; cleaned up side and front frames
    - Removed old, suppressed features.
    - Fixed endcap holes in side frames.
    - Fixed version number in side frames.
    - Updated version number from 0.8 to 0.8.1 in side/front frames.
    - Organized features into folders.
    [Cuberail_front.SLDPRT, Cuberail_side.SLDPRT]
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2018-01-29 fixed miscellaneous problems (see desc.)
    - Changed the mounting holes in the backplane to match the new pattern.
    - Fixed broken references in the inhibit board.
    - Fixed flipped label in the +X frame.
    [Backplane_board.SLDPRT, Cuberail_front.SLDPRT, Inhibit_board.SLDPRT]
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2018-01-30 fixed to the correct density
    I hadn't actually tweaked the density to approximate a stuffed board,
    like I said in the last commit.
    [Backplane_board.SLDPRT, Generic_board.SLDPRT, Solar_board.SLDPRT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]
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2018-02-07 Updated display stand, added vibration holder, added helical static reflector cone.
    [Assembly.SLDASM, Bolt.SLDPRT, Cubesat Mounting Assembly.SLDASM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]
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2018-02-11 backplane no longer shares mounting holes w/ solar
    [Cuberail_back.SLDPRT]
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2018-02-12 moved the backplane standoffs
    This avoids having screws coming into a hole from both ends. (The other
    screw came from the solar board.)
    [Backplane_board.SLDPRT, Cuberail_back.SLDPRT, M2x4_vented_93235A302_VENTED 18-8 SS SOCKET HEAD CAP SCREW.SLDPRT]
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2018-03-05 reworked the board to not be one giant sketch
    [GenericCard.SLDASM, GenericCard_board.SLDPRT]
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2018-06-07 fixed solar board; added spring card
    reaction wheel motor mounts need clearance from the SMD springs
    [Solar_board.SLDPRT, Solar_card.SLDASM, springCard.SLDASM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]
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2018-06-11 Bumped version numbers to 1.0.0 for first order!
    To clarify, we're ordering aluminum versions of these parts, not working
    for the First Order...
    [Cuberail_back.SLDPRT, Cuberail_front.SLDPRT, Cuberail_side.SLDPRT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]
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2018-07-18 Tweaked positions of the spring pins and lip
    The spring pins now have an adequate margin away from the thermal contact area,
    so that they won't bleed solder into it. The thermal contact area has been expanded
    to account for the tolerance in the card slot. These changes brought the pins very
    close to the edge of the lip. So, the lip was extended by 0.3 mm and the version
    number on the side panels was bumped to 1.0.1.
    [Cuberail_side.SLDPRT, GenericCard.SLDASM, GenericCard_board.SLDDRW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]
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2018-07-18 fixed the upside down shelves
    I actually just flipped the Z springs to the other end, since that's easier, lol.
    [Cuberail_front.SLDPRT, Rail_assembly.SLDASM]
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2018-08-21 fixed rebuild error in Cuberail_front, propagated the fix into assemblies
    [Backplane.SLDASM, Camera_card.SLDASM, Cuberail_front.SLDPRT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]
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2018-09-07 added new Molex RF connectors and fixed screw mates in top level assembly
    [100211587UGM000_B.2.sldprt, 12pin_connector.SLDPRT, 12pin_male_rightAngle_1515012X601XXX_100211589MOD000B.SLDPRT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]
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2018-12-17 replaced the solar connectors
    This new pair will allow the endcards to slide in without hitting the
    frames.
    [GenericCard_board.SLDPRT, Solar_board.DXF, Solar_board.SLDPRT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]
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2018-12-22 fixed weird discrepancies in endcaps and structure
    The "back" frame had a different fillet radius between the rail and main
    body than the "front" frame.
    [Cuberail_back.SLDPRT, endcap.SLDPRT, endcap_Zneg.DXF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]
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2019-01-06 renamed some assembly directories
    I still need to make a decision on how to organize the +/-Z things...
    This is for issue 25 on the GitHub repo.
    [100211647UGM000_B.1.sldprt, 2x22_Female(A3D-44DA-2DSE(71)).SLDPRT, 2x22_Male(A3B-44PA-2DS(71)).SLDPRT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]
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2019-04-02 added new drawings for x frames, fixed minor bug in frames asm
    [Frame_+X.SLDDRW, Frame_-X.SLDDRW, Frame_Y.SLDDRW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]
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2019-04-06 fixed general card size, updated frame drawings again
    [+X.SLDDRW, -X.SLDDRW, Endcard.SLDASM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]
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2019-04-11 fixed generic card name, added an rf config to GenericCardDef
    [Assem1.SLDASM, Backplane.SLDASM, Backplane_board.SLDPRT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]
2019-04-11 fixed backplane dxf, center mount holes were off
    [Backplane_board.DXF]
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2019-04-12 minor fixes, made -Z endcard asm, added bolts to solar asm
    [ALTA-FIVE-CELL-THROUGH-SLOT.sldprt, Assem2.SLDASM, EndCard.SLDPRT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]
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2019-04-22 added spring screws to frames assembly, started new frame drawings, minor fixes
    [+X.SLDDRW, +X_Frame.SLDDRW, 84985A460_SHORT LENGTH SS LONG-NOSE SPRING PLUNGER.SLDPRT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]
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2019-05-06 add interference fit dowl pins on x+/- frames
    [+X_Frame.SLDDRW, -X_Frame.SLDDRW]
2019-05-09 added missing fillets, made readonly step/sldprt parts for each frame piece
    [+X_Frame.SLDDRW, +X_Frame.SLDPRT, -X_Frame.SLDDRW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]
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2019-05-12 fixed build space sketch in generic card def
    [GenericCardPCBDefinition.DXF, GenericCardPCBDefinition.SLDPRT, GenericCardPCBDefinitionNoRF.DXF]
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2019-05-19 new battery card design. batteries turned to avoid threaded tabs on frame
    [93625A101_TYPE 18-8 STAINLESS STL NYLON-INSERT LOCKNUT-1.SLDPRT, Battery Holder 2.0.SLDPRT, Battery Holder 2.1.SLDPRT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]
2019-05-19 updated backplane v3 and backassembly with correct hole location
    [BackplaneBoardPCBv3.DXF, BackplaneBoardPCBv3.SLDPRT, backplaneassembly.SLDASM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]
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2020-05-10 updated mass of components, working on coordinate system fix
    [91292A032_TYPE 18-8 SS SOCKET HEAD CAP SCREW.SLDPRT, 91585A343_18-8 STAINLESS STEEL DOWEL PIN.SLDPRT, 91732A183_SPARK PLUG THREAD REPAIR KIT.SLDPRT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]
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2020-06-23 Updated OTRA card, swapped C3 and Star Tracker
    [DxWiFiCard.SLDASM, OTRACard.SLDASM, OTRA_M12.SLDPRT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]
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2020-07-08 Fixed -Z End Cap and modified turnstile to fit.
    [EndCapPCB.SLDPRT, EndCardPCB.SLDPRT, TFM_120_01_L_D_RA.sldasm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]
2020-07-08 Fixed a missing fillet and updated main assembly.
    [EndCapPCB.SLDPRT, Endcap.SLDASM, PosEndCard.SLDASM]
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2020-07-09 Aligned generic card with origin, added 2 to OreSat0 Assembly, and fixed some mates.
    [CardwithConnectors.SLDASM]
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2020-07-12 Fixed vibration jig file structure and removed temp files.
    [.25in_Al_plate_1U.SLDPRT, CorkStrip_1U.SLDPRT, OreSat Vibration Fixture XY 1U axis.SLDDRW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]
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2020-07-16 Made 1U +X drawing, slightly fixed -X drawing, added missing fillet to 1U frames.
    [+X_1UFrame.SLDDRW, -X_1UFrame.SLDDRW, 1UFrame.SLDPRT]
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2020-07-18 Made some fixes to 1U drawings and fixed end card screw depth.
    [+X_1UFrame.SLDDRW, -X_1UFrame.SLDDRW, Y_1UFrame.SLDDRW]
2020-07-19 Corrected -X and Y drawings and fixed anodization type on all 1U drawings.
    [+X_1UFrame.SLDDRW, -X_1UFrame.SLDDRW, Y_1UFrame.SLDDRW]
2020-07-20 Increased drawing scale to 1:1, added some missing datums, fixed tolerences.
    [+X_1UFrame.SLDDRW, -X_1UFrame.SLDDRW, Y_1UFrame.SLDDRW]
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2020-07-24 Changed drawing tolerances and added a new revision for manufacture, and updated 1U build folder.
    [+X_1UFrame.SLDDRW, -X_1UFrame.SLDDRW, Y_1UFrame.SLDDRW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]
2020-07-24 Exported 1U vibration jig files into STEP and pdf for manufacturing.
    [OreSat Vibration Fixture XY 1U axis.SLDDRW, OreSat Vibration Fixture XY 1U axis.SLDPRT, OreSat Vibration Fixture XY 1U axis.STEP]
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2020-08-02 Added endcap clearance between rails and solar boards.
    [1UFrames.SLDASM, EndCapPCB.SLDPRT, Endcap.SLDASM]
2020-08-02 Enlarged solar screw holes to loose fit to ensure solar connectors align.
    [SolarModulePCB.SLDPRT]
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2020-08-07 Made new CFC assembly and fixed some mates in 2U frames.
    [CFCcard.SLDASM, CFCcard.SLDPRT, DxWiFiCard.SLDASM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]
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2020-08-19 Updated cards with tolerances to allow more room between +X and -X frames.
    [GenericCardPCBDefinition.DXF, GenericCardPCBDefinition.SLDPRT, GenericCardPCBDefinitionNoRF.DXF]
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2020-08-20 Added new OreSat1 step file and fixed gitignore problem.
    [EndCapPCB.SLDPRT, SolarModulePCB.SLDPRT]
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2020-08-20 Added tolerance to the Star Tracker/OTRA camera mounts.
    [OTRAboardmount.SLDPRT, startracker.SLDASM, startrackerboardmount.SLDPRT]
2020-08-20 Cleaned up endcard corners and fixed battery board PCB error.
    [1U+Zendcard.SLDASM, 1UFrames.SLDASM, BatteryPCB.SLDPRT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]
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2020-08-24 updated frames and backplane for new card slot locations, added battery assembly, fixing issues
    [BackplaneBoardPCB.SLDPRT, C3Card.SLDASM, CDS_v13_Maximum_spec.SLDPRT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]
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2020-08-25 Fixed 1U end caps and made new DXFs, updated in OreSat0, and fixed names battery card subassemblies.
    [1U+ZEndCapPCB.DXF, 1U+Zendcard.SLDASM, 1U-ZEndCapPCB.DXF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]
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2020-08-27 updated posts and removed solar holes in frames and fixed mate in OreSat
    [Frames.SLDASM]
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2020-08-29 Fixed a tolerance issue on the -Z endcap.
    [1U-ZEndCapPCB.DXF, 1UEndCapPCB.SLDPRT]
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2020-08-29 Removed an extra connector and fixed a broken mate.
    [1U+Zendcard.SLDASM]
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2020-09-03 Fixed battery card inhibit switch mates and made pressed/unpressed configurations.
    [InhibitSwitchAssembly.SLDASM]
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2020-09-09 Fixed a referencing problem with the 2U endcaps.
    [EndCapPCB.SLDPRT]
2020-09-09 Replaced too long fastener with fastener of appropriate length.
    [92095A276_BUTTON HEAD HEX DRIVE SCREW.SLDPRT, BatteryPCB.SLDPRT, InhibitSwitchAssembly.SLDASM]
2020-09-09 Increased spring pin tap depth by 2mm to compensate for manufacturing errors.
    [+X_1UFrame.SLDDRW, -X_1UFrame.SLDDRW]
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2020-09-13 Fixed 1U endcard problem with new circular deployer.
    [1U+Zendcard.SLDASM, 1UEndCapPCB.SLDPRT, 1UEndcap.SLDASM]
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2020-09-14 Replaced endcap fastener with 4mm version to try to standardize fasteners.
    [1UEndcap.SLDASM, m55-6001242_asm.SLDASM]
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2020-09-17 halfway fixed inhibit switch/battery card issues. updated some cfc stuff and lens mount drawing
    [BatteryPCB.SLDPRT, CFCCard.SLDASM, CFClens.SLDPRT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]
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2020-09-17 updated battery card inhibit switch assemblies, fixed some funky oresat live stuff maybe
    [90965A110_TYPE 316 STAINLESS STEEL FLAT WASHER.SLDPRT, BatteryPCB.SLDPRT, D2F_L3_D.SLDASM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]
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2020-09-23 updated reaction wheels and magnetorquer issues, fixed oresatlive issues, put in jims new helical cad, and steves cfc sensor cad
    [91292A032_TYPE 18-8 SS SOCKET HEAD CAP SCREW.SLDPRT, 93395A135_REACTION WHEEL TYPE 316 SS FLAT-HEAD SOCKET CAP SCREW.SLDPRT, 93395A138_REACTION WHEEL TYPE 316 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]
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2020-09-30 Incresed tolerances and removed space foam cutout on generic card.
    [CardwithConnectors.SLDASM, DxWiFiCard.SLDASM, GenericCardPCBDefinition.SLDPRT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]
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2020-10-01 Fixed battery card keepouts and inhibit switch mates.
    [BatteryPCB.SLDPRT, inhibitswitch.SLDASM]
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2020-10-08 Added 2 more fasteners, fixed CFC heatsink material.
    [93235A301_VENTED 18-8 SS SOCKET HEAD CAP SCREW.SLDPRT, 94100A150_18-8 SS PRESS-FIT NUT FOR SOFT MTL PLASTIC.SLDPRT, sensor.SLDPRT]
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2020-10-18 Added chamfers to the circular deployer and fixed a whole bunch of errors.
    [1U+Zendcard.SLDASM, 1UEndCapPCB.SLDPRT, 1UEndCardPCB.SLDPRT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]
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2020-10-23 Added melt wire holes and boss locations to mezzanine board.
    [1U+Zendcard.SLDASM, MezzaninePCB.DXF, MezzaninePCB.SLDPRT]
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2020-11-13 added new configurations for inhibitswitches to flip plunger
    [inhibitswitch.SLDASM]
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2020-11-22 Fixed a bad extrude in the +X cutout configuration
    [CardWedge.SLDPRT]
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2020-12-23 Updated drawing tolerances, added wire wrapping jig, updated hardware specs
    [92290A015_TYPE 316 SS SOCKET HEAD CAP SCREW.SLDPRT, ADACSCard.SLDASM, Bracket_Base_Short.SLDDRW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]
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2021-01-19 Fixed Kapton tape lengths and some deployed config errors
    [EndCardPCB.SLDPRT, Helical Antenna.SLDPRT, HelicalDeployerBiggerSpringBiggerDowel.SLDASM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]
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2021-02-17 Fixed error causing 2u pos endcard to save in deployed state when it wasnt supposed to
    [HelicalDeployerBiggerSpringBiggerDowel.SLDASM]
2021-02-17 Removed relations causing errors and fixed components in pos endcard in order to export x_t
    [HelicalDeployerBiggerSpringBiggerDowel.SLDASM]
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2021-02-20 Added stowed states for individual elements, new burnwire holder
    [1U+Zendcard.SLDASM, 1UEndcap.SLDASM, BurnwireHolder.SLDPRT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]
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2021-03-05 Updated turnstyle deployer to have burnwire guide included in one part, reduced trapdoor height thickness
    [1U+Zendcard.SLDASM, TapeMeasureMount.SLDPRT, Trapdoor.SLDPRT]
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2021-03-07 Added square washer to be used for clamping burnwire down more easily
    [squarewasher.SLDPRT]
2021-03-07 Changed turnstile deployer, extra long burnwire track towards resistor, ribbed trapdoors, changed heights and locations of antenna mounts
    [1U+Zendcard.SLDASM, TapeMeasureMount.SLDPRT, Trapdoor.SLDPRT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]
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2021-03-08 Updated PCB's for manufacture, increased tolerance around turnstyle deployer, added notations for where antennas contact pcb
    [1U+Zendcard.SLDASM, 1UEndCapPCB.SLDPRT, 1UEndCardPCB.SLDPRT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]
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2021-03-24 Reduced tolerance to 0.1mm for all wedges and triangles aside from posXcutout
    [CardWedge.SLDDRW, CardWedgePosX.SLDDRW, CardWedgePosXShort.SLDDRW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]
2021-03-24 Updated radius to document tolerance on positivex cardwedge drawings
    [CardWedgePosX.SLDDRW, CardWedgePosXShort.SLDDRW]
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2021-03-25 Added 0.5mm roundover to batteryholder cad to prevent pinching of kapton heaters
    [BatteryHolderBottom.SLDPRT]
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2021-03-25 Added tolerances to turnstyle deployer and top cap, tolerances for antennas connecting to board done with fillets
    [1U+Zendcard.SLDASM, TapeMeasureMount.SLDPRT, topCap.SLDPRT]
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2021-03-26 Updated turnstyle mount to have more fillets to avoid cracking
    [1U+Zendcard.SLDASM, TapeMeasureMount.SLDPRT, topCap.SLDPRT]
2021-03-26 Added broken edges to squarewasher and increased trench width of tapemeasuremount
    [TapeMeasureMount.SLDPRT, squarewasher.SLDPRT]
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2021-03-29 Added more tolerance to the topCap part's underside
    [1U+Zendcard.SLDASM, topCap.SLDPRT]
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2021-04-11 Added slots instead of holes for CFC thermal straps, fixed missing part
    [90910A912_BUTTON HEAD TORX SCREWS.SLDPRT, OresatliveMountBreakdown.SLDASM, thermalStrap.SLDPRT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]
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2021-04-13 Replaced 18-8 Washers with 316SS washers in +z endcard assem
    [1U+Zendcard.SLDASM]
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2021-04-13 Updated +z 1U burnwire resistor height and other mating relations to fully define assembly
    [1U+Zendcard.SLDASM, PAC01_VIS.SLDPRT]
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2021-04-15 Increased tolerance on topcap, reduced axle diameter on trapdoor, updated fillets on tapemeasuremount
    [TapeMeasureMount.SLDPRT, Trapdoor.SLDPRT, topCap.SLDPRT]
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2021-05-02 Added Prototype 2U turnstile and corrected helical jig files
    [Door.SLDPRT, Turnstile.SLDPRT, baseSegment.STL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]
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2021-05-13 Modified CFC pin locations, added fiberglass washer insulators, changed TIM color to black, fixed minor interference issues, modified thermal mass connection to lens mount, and adjusted TIM thickness
    [93493A312_FIBERGLASS FLAT WASHER.SLDPRT, CFCcard.SLDPRT, arcClampTIM.SLDPRT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]
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2021-05-17 Modified CFC subassembly to fix tolerance issues and add changes
    [91217A011_HIGH HOLD CONE POINT SET SCREW.SLDPRT, 96025A268_CLIPPED WASHER.SLDPRT, CFCcard.SLDPRT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]
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2021-05-18 Added Emmy's fix to oresat live mount errors, fixed fastener now registering on main oresat assembly
    [DxWiFiCard.SLDASM, Endcap.SLDASM, OresatliveMountBreakdown.SLDASM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]
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2021-05-24 Added fastners and burn wire location for turnstile
    [EndCardPCB.SLDPRT, M2x8_torx_90910A923_LOW-PROFILE BUTTON HEAD TORX MACHINE SCREW.SLDPRT, TFM_120_01_L_D_RA.sldasm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]
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2021-06-17 Changed reaction wheel fasteners to be button head cap screws for clearance issues
    [90910A921_LOW-PROFILE BUTTON HEAD TORX MACHINE SCREW - Copy.SLDPRT, 90910A923_LOW-PROFILE BUTTON HEAD TORX MACHINE SCREW.SLDPRT, MountingBeamV2.SLDPRT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]
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2021-06-30 Fixed naming convention issue and broken OreSat1B assembly
    [PeriscopeHASPAsssembly.SLDASM, PosEndCard.SLDASM, mountingBracket.SLDPRT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]
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2021-07-04 Added higher res oresat live camera board cad and fixed mates, and hid some sketches on one fastner and DxWifi board
    [92290A012_TYPE 316 SS SOCKET HEAD CAP SCREW.SLDPRT, DxWiFiCard.SLDASM, OresatliveMountBreakdown.SLDASM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]
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2021-07-31 Fixed the mounting bracket issue with the 3U, trying new design for OreSat Live mounting system
    [94669A096_ALUM UNTHRD SPACER.SLDPRT, ADACSCard.SLDASM, CFCcard.SLDPRT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]
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2021-08-05 added 1.5U backplane assembly, added card slots in the ADCS area on 1.5U frames, corrected star tracker cutout on 1.5U, corrected 1.5U solar card dissymmetry, updated ADCS card by removing 20 pin con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
    [1.5UBackplaneAssembly.SLDASM, 1.5UBackplanePCB.SLDPRT, 1.5UFrame.SLDPRT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]
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2021-08-06 added 1.5U backplane assembly, added card slots in the ADCS area on 1.5U frames, corrected star tracker cutout on 1.5U, corrected 1.5U solar card dissymmetry, updated ADCS card by removing 20 pin con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
    [1.5UFrame.SLDPRT, 1.5UFrames.SLDASM, ADACSCard.SLDASM]
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2021-08-08 renamed ALL THE THINGS
    COTS parts are now broken up into subfolders. Spaces have been removed
    from file names.
    [100211587UGM000_B.2.sldprt, 100211647UGM000_B.1.sldprt, 100211647UGM000_B.1_40pin.sldprt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]
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2021-08-09 Reworked new magnetorquer into one assembly and integrated into the oresat assembly
    [Any_BatteryAssembly.SLDASM, Any_MagnetorquerClamp.SLDPRT, Any_MagnetorquerComplex.SLDASM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]
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2021-08-10 Added mounting fasteners for magnetorquer complex, waiting on quote for rods to fix collision issues
    [Any_BatteryAssembly.SLDASM, Any_MagnetorquerComplex.SLDASM, Any_MountingBeam.SLDPRT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]
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2021-08-10 Added washers to battery card, replaced PEEK washer with SS in CFC, replaced card fasteners with torx in StarTracker
    [Any_BatteryAssembly.SLDASM, Any_BatteryPCB.SLDPRT, Any_InhibitSwitch.SLDASM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]
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2021-08-16 rearranged RF connectors on 1U backplane, replaced debug connector on 1U with new 16 pin connector (female on board) and added right angle connector for new debug pcb; connector is not centered in de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
    [1U_BackplaneAssembly.SLDASM, m55-6001642_asm.stp, m55-7101642_asm.stp]
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2021-09-18 Added debug connector and debug connector cutout to 1.5U assembly and backplane. Very low clearance
    [1.5U_BackplaneAssembly.SLDASM, 1.5U_BackplanePCB.SLDPRT, 1.5U_Frame.SLDPRT]
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2021-09-27 Finished new 2U drawings, removed old 2U drawings, reverted new 2U drawings to naming convention.
    [2U_Y.SLDDRW, 2U_Y_new.SLDDRW, 2U_minusX.SLDDRW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]
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2021-11-03 Oresat 0.5 cad is UP TO DATE! Turnstile antennas added in -Zendcard, 1.5U-Zendcap configuration added, all connectors swapped and rotated to fit.
    [OreSat0.5_-Zendcard.SLDASM, OreSat0.5_Endcap.SLDASM, OreSat0_Endcap.SLDASM]
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2021-11-13 fixed 1.5U endcaps and created new PCB part, there are still CAD inconsistencies in 1U, 2U, and 3U endcaps, unused configurations, missing holes for endcap cnnectors, etc.
    [OreSat0.5_-Zendcard.SLDASM, OreSat0.5_EndCapPCB.SLDPRT, OreSat0.5_Endcap.SLDASM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]
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2021-11-16 Corrected ALL endcaps. Endcap connector is now male (M55-7011242R) and endcard connector is now female (M55-6001242R). All endcards now have connector allignment holes modeled. The 3U still uses the 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
    [OreSat0.5_EndCapPCB.SLDPRT, OreSat0.5_Endcap.SLDASM, OreSat0_EndCapPCB.SLDPRT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]
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2021-12-15 Modified inhibit design from 3.5 to 4.5mm pin diameter, in addition to tighter tolerances on inhibit cutouts on frames
    [OreSat_InhibitClamp.SLDPRT, OreSat_InhibitPin.SLDPRT]
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2021-12-20 Implemented all changes in 1.5U design review - prepared frames to be shipped, cad is up to date except for material properties. Changed rail ends to chamfer instead of fillet, removed generic card, 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
    [1.5U_BackplaneAssembly.SLDASM, 1.5U_Frame.SLDPRT, 1.5U_Frames.SLDASM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]
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2022-02-04 Updated reactionwheel machining bracket to hold 2 parts and be better toleranced
    [Machining_fixture_assembly.SLDASM, OreSat_MountingBeam.SLDPRT, machining_fixture_part.SLDPRT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]
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2022-03-01 fully revised helical deployer CAD, using better burnwire clamps, adjusted lid and base sizes
    [BurnwireBlock.SLDPRT, BurnwireClamps.SLDASM, BurnwireSquareWasher.SLDPRT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]
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2022-03-02 fixed mates and added indicator for solder patch of helical antenna to endcard pcb
    [OreSat_EndCardPCB.SLDPRT]
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2022-04-29 Same as my last but fixed naming conv.
    adding the capstones work on the frames to the master branch, now it has the name of the folder seperated by underscores instead of spaces
    [2U_Assembly_v2.SLDASM, 90910A920_Button Head Torx Screws.SLDPRT, Wedge_v2.SLDPRT]
2022-04-30 Made lots o changes to v2 Frames
    -Was supposed to change lattice cuts to 4mm, but would collide with screw so kept at 4.5mm
    -Remade the Card guidance nubbins on the plus x
    -Chamfered the back of the wedges to guide cards on +X
    -Removed Vent Slots to promote symmetry
    -Changed Frames to M2 screws but it may be useless, will elaborate at design review
    -Redid entire assembly since it changed so much with changes I made, everything is neat and tidy in folders
    [2U_Assembly_v2.SLDASM, 90128A181_Zinc-Plated Alloy Steel Socket Head Screw.SLDPRT, Wedge_v2.SLDPRT]
2022-05-05 Design Review Changes!!!
    -Changed frame connecting screws back to M2.5
    -Changed all taps to straight through, instead of bottoming
    -Shrank the Y frame screw pillars
    -Moved the M2 tapped screw holes on the wedges to the center
    -Filleted the lattice cuts ~ Looks cool!
    +Still need to adjust slots for new wedge hole location
    +Assembly blew up, need to redo
    [2U_Assembly_v2.SLDASM, OreSat_GenericCardPCBDefinition.SLDPRT, Wedge_v2.SLDPRT]
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2022-05-13 Fixed Assembly, added fillet to ramps, updated version #
    After I reached out to a local machine shop they told me to add some fillets where the ramps meet the base of the frame. I updated the verison numbers to 2.0.0, and did todays date becuase hopefully they get sent out to be manufactured today. Also I added a fillet to the wedges, since with the new fillet on the ramp, they would collide without it. The assembly isnt fully complete, I still need to add some fasteners, but as of now there are no new conflicts due to the design change, there are old conflicts, like the bottom star tracker and the battery, and the reaction wheels with eachother, but nothing new.
    [2U_Assembly_v2.SLDASM, Wedge_v2.SLDPRT]
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
